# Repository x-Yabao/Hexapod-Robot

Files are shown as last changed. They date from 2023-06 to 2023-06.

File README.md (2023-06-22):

# Hexapod-Robot
这是一个六足机器人创客项目，以宫崎骏的电影《哈尔的移动城堡》作为灵感。由于资金非常有限，并且项目在家里完成，工具也非常有限，所以整个项目的设计思路是，保持机器人具有一定运载能力的同时，使用低成本硬件，并且尽量使用现成零件，减少加工需求。通过这个GitHub仓库，可以很方便地对整个项目进行复现，包括机械设计、电子设计以及程序设计，整个项目成本在1000块左右，如果你感兴趣的话，那就赶紧动起手来吧~

项目视频请移步 [bilibili](https://www.bilibili.com/video/av64897985/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) 观看。

<p align='center'>
    
</p>

<p align='center'>
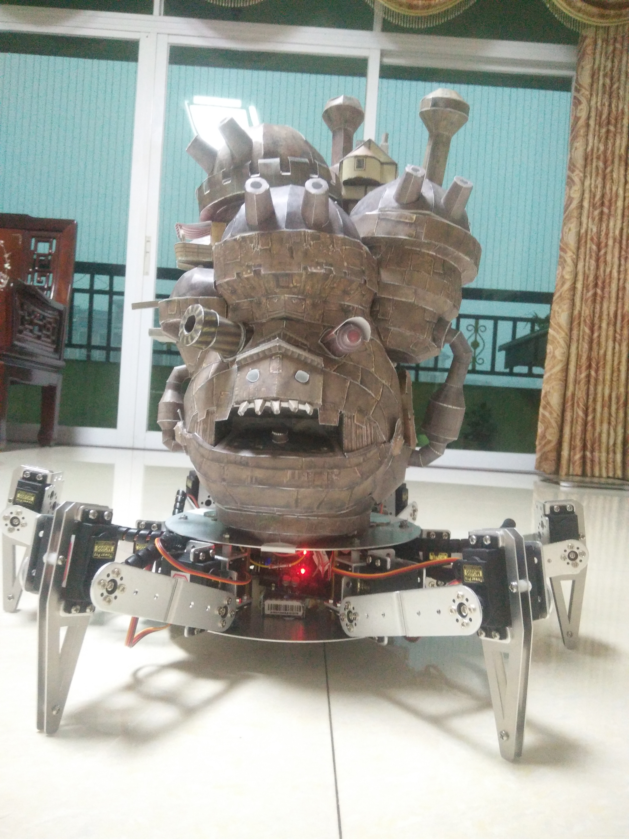
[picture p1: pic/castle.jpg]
    
</p>

---

## 详细介绍 & 使用指南

请移步到我的 [CSDN 博客](https://blog.csdn.net/coolyabao/article/details/100145744) 查看吧。

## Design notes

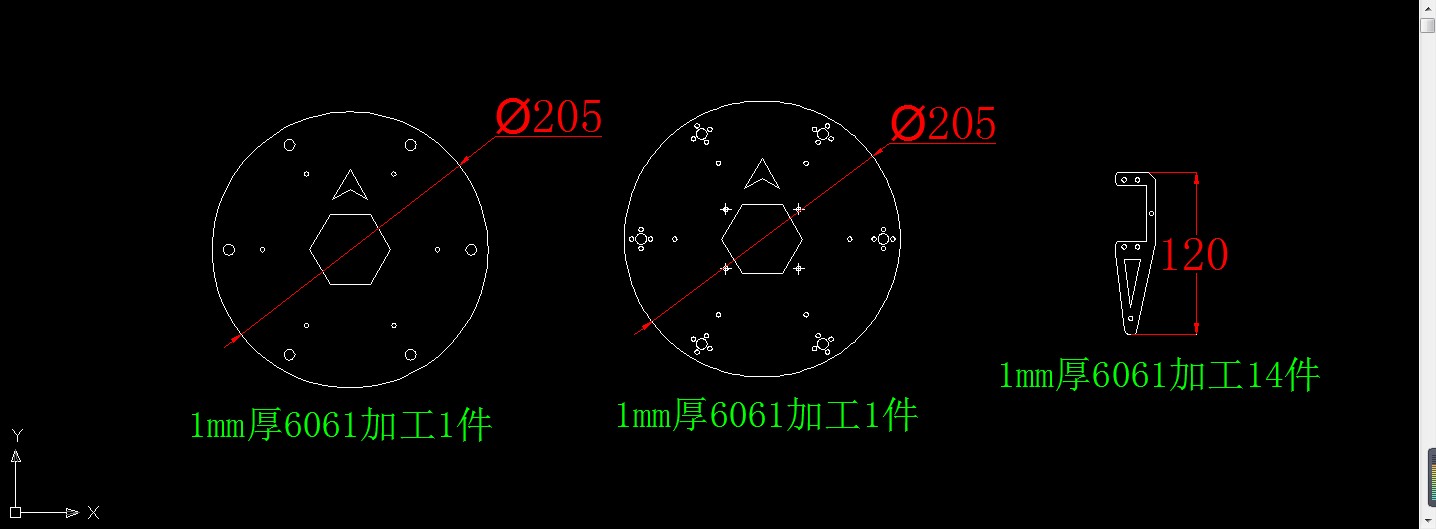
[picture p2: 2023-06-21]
加工文件/加工商家反馈图片.jpg

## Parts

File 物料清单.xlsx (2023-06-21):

六足机器人物料清单 |  |  |  |  |  |  | 总计：1023.35
机械部分
序号 | 材料名称 | 型号 | 数量 | 单价 | 总价 | 备注
1 | 舵机 | MG995 180度 | 18 | 25.5 | 459
2 | 长U支架 |  | 12 | 4 | 48 | 淘宝搜“舵机支架”，就有所需要的支架和轴承
3 | 单轴舵机支架 |  | 18 | 4 | 72
4 | 轴承 |  | 18 | 3.2 | 57.6
5 | 六角支柱 | M3*6 | 42 |  | （约）30
6 | 单头六角铜柱 | M3*60+6 | 6
7 | 螺丝 | M3*4 | 24
8 | 螺丝 | M3*6 | 84
9 | 螺丝 | M3*8 | 72
10 | 螺丝 | M3*12 | 12
11 | 螺丝 | M3*16 | 30
12 | 螺母 | M3 | 132
13 | 垫片 | M3 | 若干
14 | 上底盘 |  | 1 |  | 100 | 独自加工或者寻找商家代加工
15 | 下底盘 |  | 1
16 | 小腿支架 |  | 12
17 | 缠绕包裹线 | 8MM 2米 | 1 | 3.8 | 3.8 | 用于包裹舵机线
电控部分
序号 | 材料名称 | 型号 | 数量 | 单价 | 总价 | 备注
1 | 24路舵机控制器 | LOBOT（品牌名） | 1 | 138 | 138 | 因为本文档内的动作组文件、电路设计等是根据此型号控制板设计的，用其他型号板子可能出现不兼容的现象，因而附上购买链接：https://item.taobao.com/item.htm?spm=a1z09.2.0.0.19072e8djcMglV&id=19214924650&_u=t2ccai6lfde6
2 | 航模电池 | 7.4V 2200mah | 1 | 75 | 75 | 没有的话，需要购买专门的充电器
3 | 降压芯片 | D25XB60 | 1 | 1.25 | 1.25
4 | Arduino UNO |  | 1 | 20 | 20 | 正品和仿制品价格相差较远，仿制品也 能满足使用要求
5 | 蓝牙模块 | HC-06 | 1 | 15 | 15
6 | 升压模块 |  | 1 | 3.7 | 3.7 | 把舵机控制器的3.3V电源输出升压至9V，给Arduino供电
7 | 杜邦线
8 | 若干基本元件 |  |  |  |  | 电线、开关、电阻、电路板等等

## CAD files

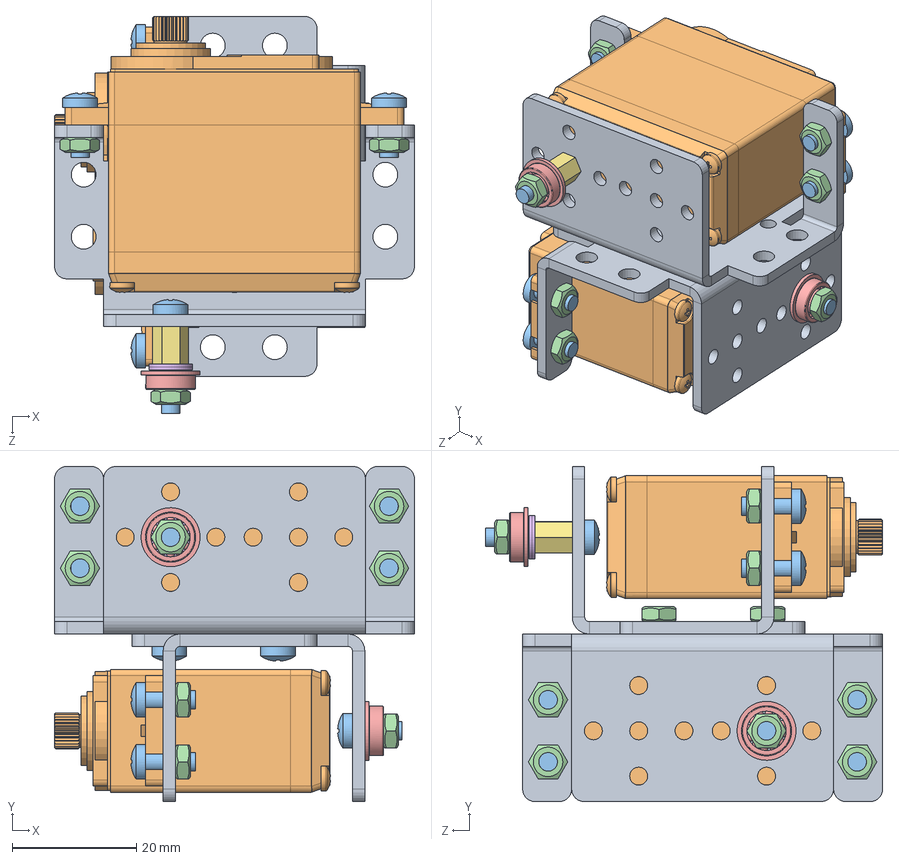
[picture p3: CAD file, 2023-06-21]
三维模型/髋关节（对称） - 装配体.SLDASM
58.0 x 54.0 x 64.0 mm
多功能支架 x 2
舵机 x 2
cross recessed pan head screws gb x 12
hex nuts, style 1-grades ab gb x 12
miniature radial ball bearings gb x 2
plain washers-n series-grade a gb x 2
六角支柱 M3x6

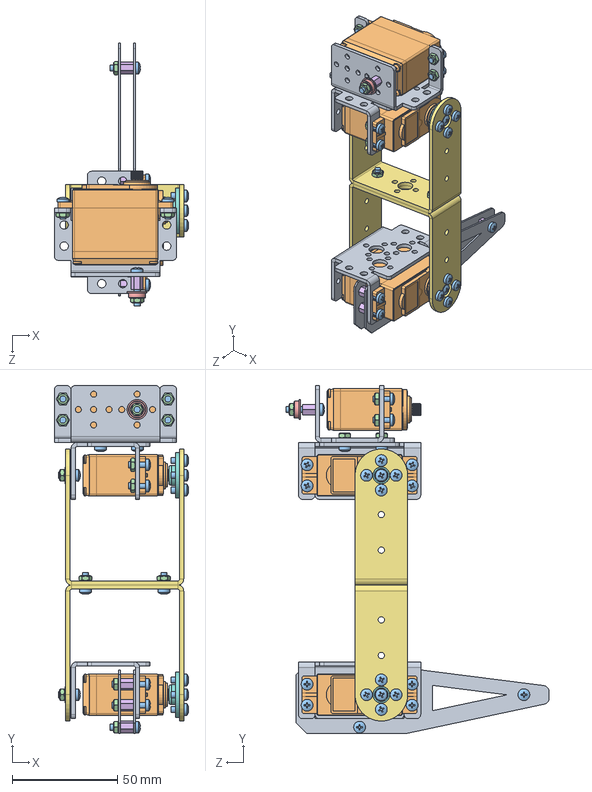
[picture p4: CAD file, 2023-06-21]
三维模型/腿部 - 装配体.SLDASM
63.8 x 165.0 x 124.9 mm
多功能支架 x 3
舵机 x 3
cross recessed pan head screws gb x 31
hex nuts, style 1-grades ab gb x 21
miniature radial ball bearings gb x 3
六角支柱 M3x6 x 7
长U型支架 x 2
舵盘 x 2
小腿支架 x 2

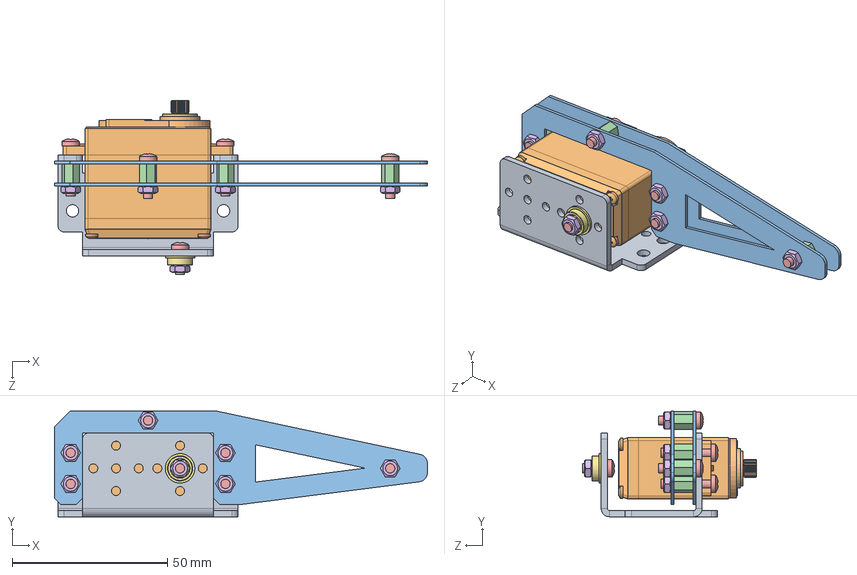
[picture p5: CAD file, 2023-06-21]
三维模型/小腿 - 装配体.SLDASM
120.0 x 34.0 x 56.0 mm
多功能支架
舵机
小腿支架 x 2
六角支柱 M3x6 x 6
cross recessed pan head screws gb x 7
hex nuts, style 1-grades ab gb x 7
miniature radial ball bearings gb

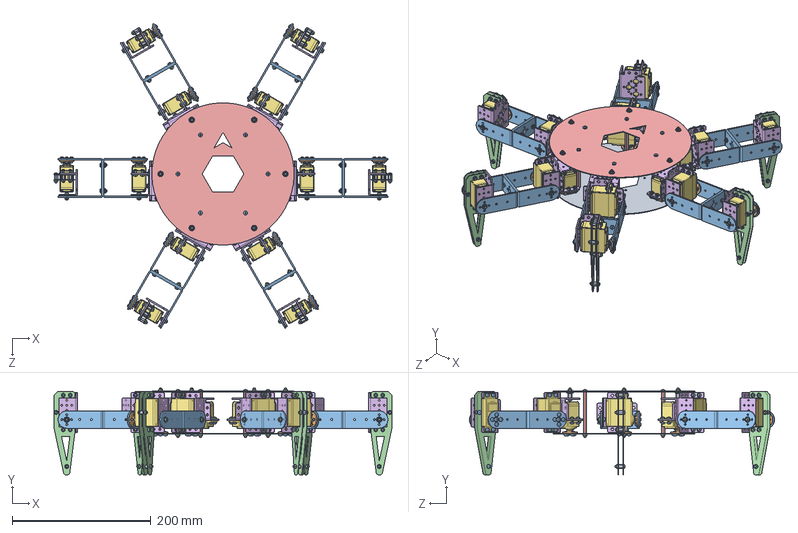
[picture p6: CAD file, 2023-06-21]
三维模型/六足机器人 1.0.SLDASM
487.2 x 124.9 x 439.6 mm
下底盘
舵盘 x 18
cross recessed pan head screws gb x 222
hex nuts, style 1-grades ab gb x 132
六角支柱（公母）M3x60x6mm x 6
多功能支架 x 18
舵机 x 18
miniature radial ball bearings gb x 18
六角支柱 M3x6 x 42
plain washers-n series-grade a gb x 12
长U型支架 x 12
小腿支架 x 12
上底板

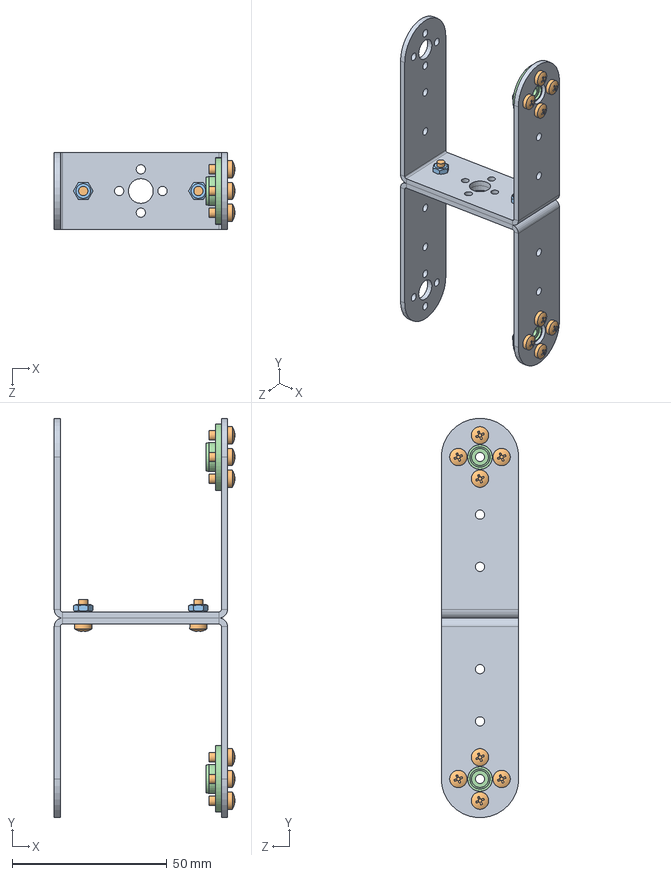
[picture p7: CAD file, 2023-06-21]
三维模型/大腿（or 大腿对称）- 装配体.SLDASM
58.4 x 128.9 x 25.0 mm
长U型支架 x 2
cross recessed pan head screws gb x 10
hex nuts, style 1-grades ab gb x 2
舵盘 x 2

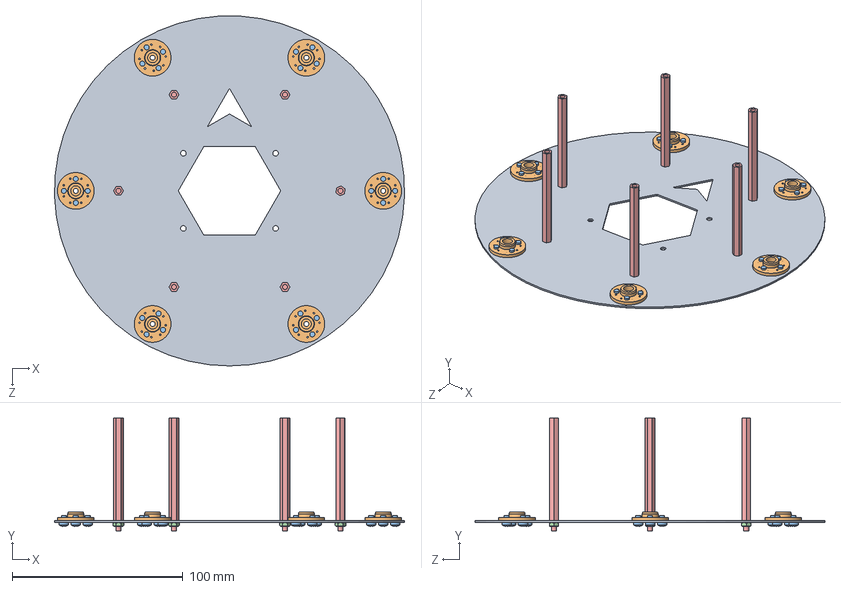
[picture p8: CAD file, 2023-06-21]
三维模型/下底盘 - 装配体.SLDASM
204.9 x 66.0 x 204.8 mm
下底盘
舵盘 x 6
cross recessed pan head screws gb x 24
hex nuts, style 1-grades ab gb x 6
六角支柱（公母）M3x60x6mm x 6

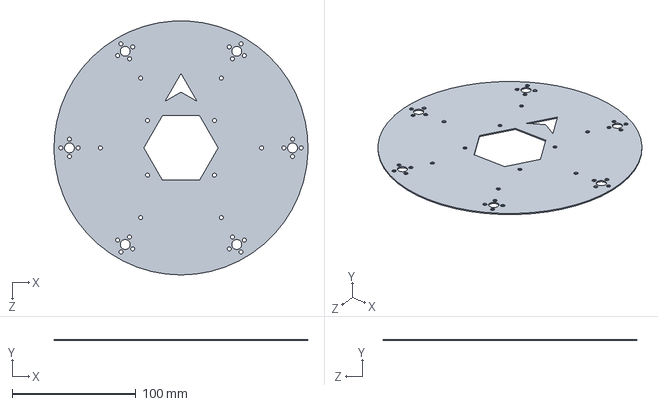
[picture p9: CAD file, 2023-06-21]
三维模型/下底盘.SLDPRT
204.9 x 1.00 x 204.8 mm

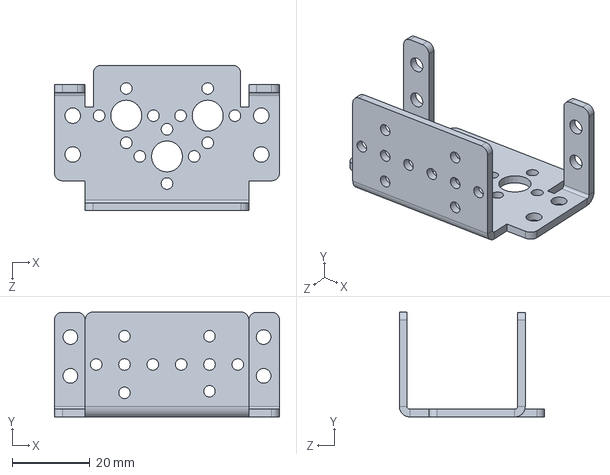
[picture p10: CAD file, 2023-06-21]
三维模型/多功能支架.SLDPRT
58.0 x 27.1 x 37.5 mm

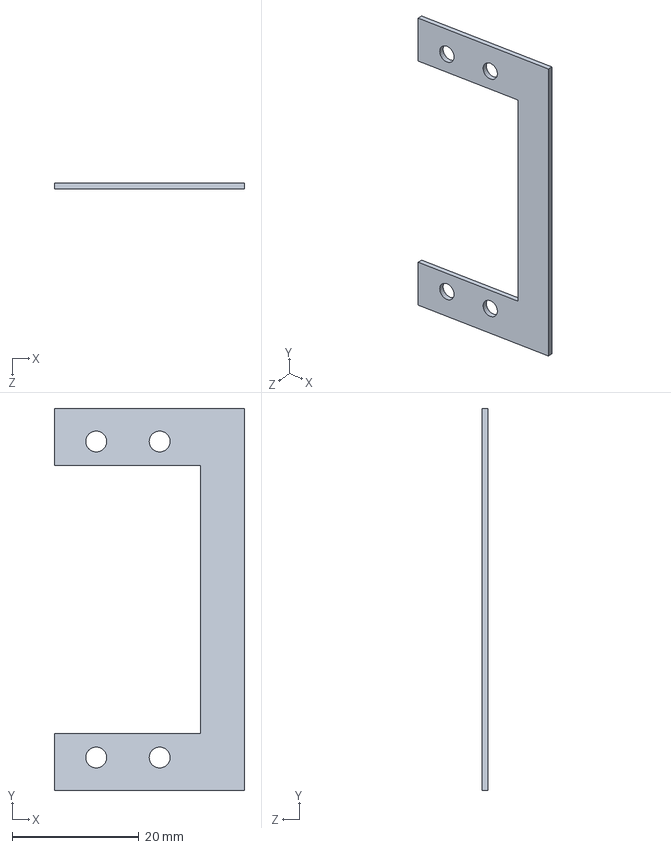
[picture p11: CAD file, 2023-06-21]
三维模型/小腿支架.SLDPRT
30.0 x 60.2 x 1.00 mm

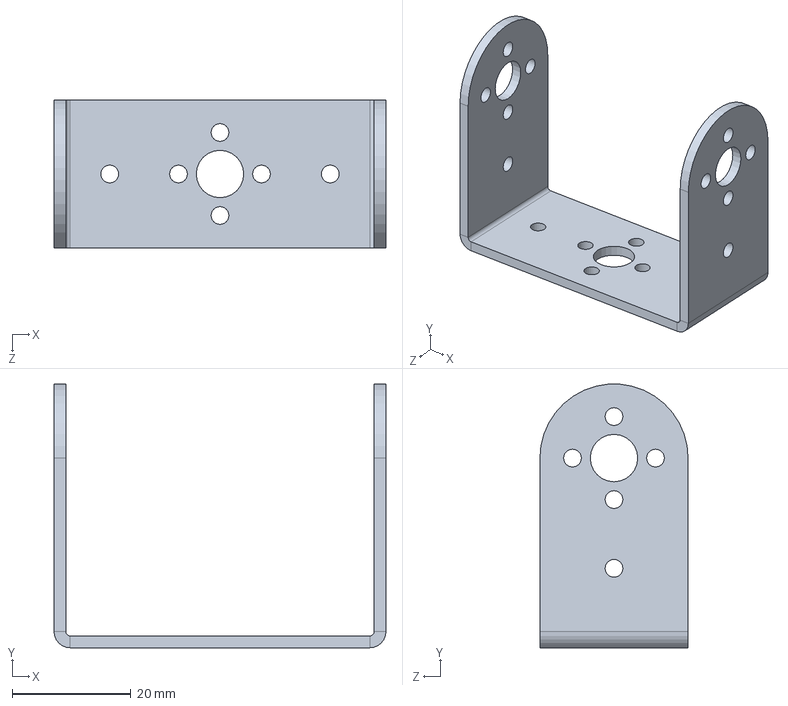
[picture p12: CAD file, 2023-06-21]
三维模型/短U型支架.SLDPRT
56.0 x 44.5 x 25.0 mm

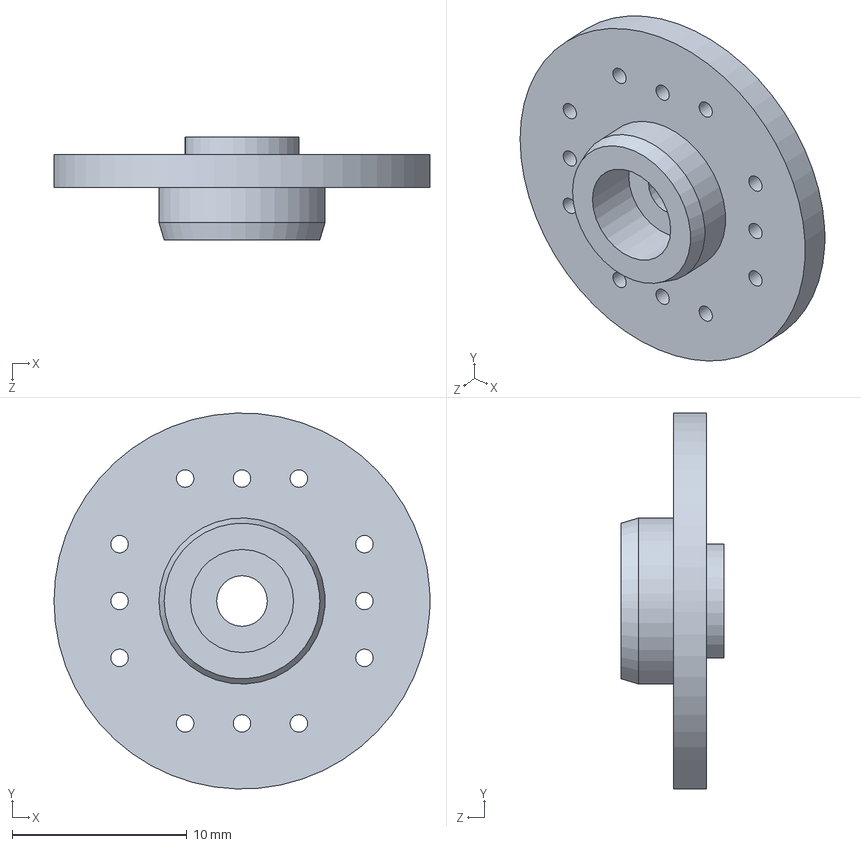
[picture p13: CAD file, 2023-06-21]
三维模型/舵盘.SLDPRT
21.5 x 21.5 x 5.90 mm

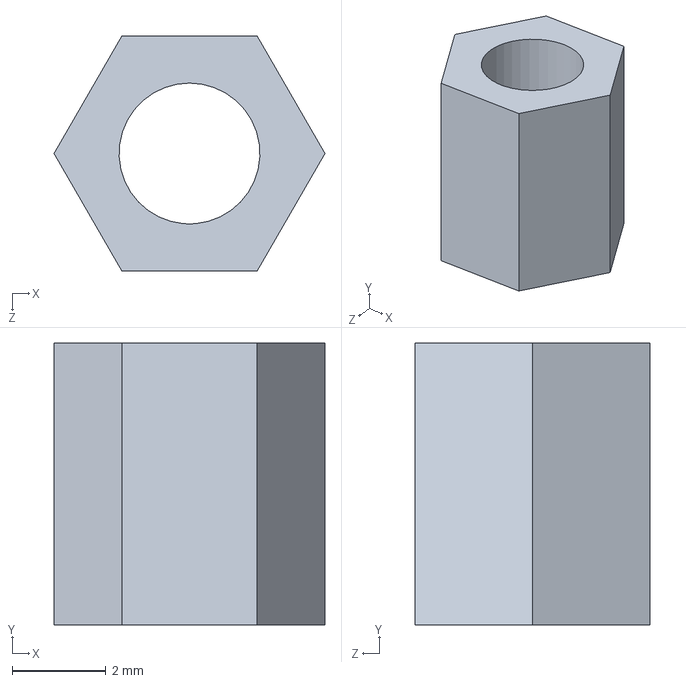
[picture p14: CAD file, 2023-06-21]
三维模型/六角支柱 M3x6.SLDPRT
5.77 x 6.00 x 5.00 mm

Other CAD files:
三维模型/髋关节 - 装配体.SLDASM
三维模型/腿部（对称） - 装配体.SLDASM
三维模型/小腿（对称） - 装配体.SLDASM
加工文件/上底板.DWG
加工文件/下底盘.DWG
加工文件/小腿支架.DWG
三维模型/上底板.SLDPRT
三维模型/六角支柱（公母）M3x60x6mm.SLDPRT
三维模型/舵机.SLDPRT
三维模型/长U型支架.SLDPRT
加工文件/上底板.SLDDRW
加工文件/下底盘.SLDDRW
加工文件/小腿支架.SLDDRW
